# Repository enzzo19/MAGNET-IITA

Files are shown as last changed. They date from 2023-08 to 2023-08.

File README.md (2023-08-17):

# MAGNET-IITA SALTA 2023

Hola soy Enzo ! el Profe mentor del equipo IITA SALTA representando al [Instituto de Innovacion y Tecnologia Aplicada(IITA)](https://iita.com.ar/salta/) en la competencia [CANSAT](https://www.argentina.gob.ar/ciencia/sact/cansat-argentina) organizada por la el Ministerio de Ciencia, Tecnología e Innovación (MINCyT) y la Comisión Nacional de Actividades Espaciales [CONAE](https://www.argentina.gob.ar/ciencia/conae) en su edicion del año 2023, la idea de este repositorio es poder tener un lugar donde puedan encontrar el proceso y evolucion que fue siguiendo el equipo para cada una de las etapas de nuestra propuesta de CANSAT en su mision MAGNET-IITA.

## Etapas por describir

    * Presentacion / Mision Secundaria.
    * Diseño / Sistema de Descenso
    * Construccion
    * Estacion Terrestre
    * Pruebas

## Presentacion

El equipo IITA-Salta esta compuesto por los siguientes integrantes.

* **Gabriel Gutierrez**
* Rol en el equipo:
  * Encargado de Construccion
  * Encargado de Electronica

<p 
align="center">
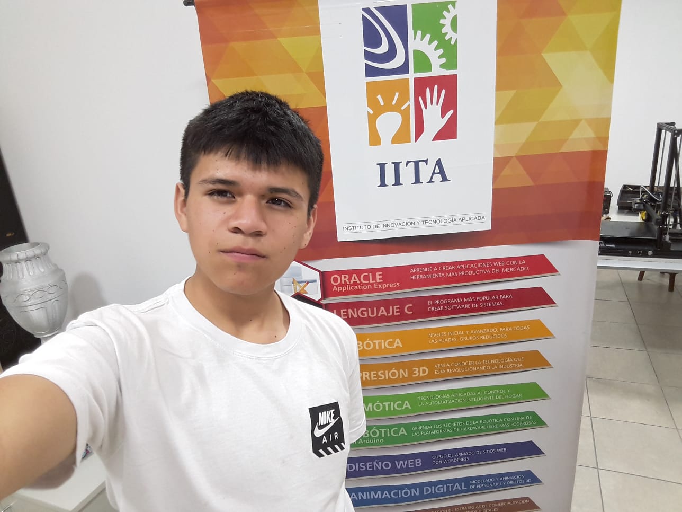
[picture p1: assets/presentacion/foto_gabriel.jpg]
Foto Gabriel

</p>

* **Morena Piren Castellanos**
* Rol en el equipo:
  * Encargado de Diseño 3D
  * Encargado de Sistema de Descenso
  * Ayudante de Construccion

<p 
align="center">
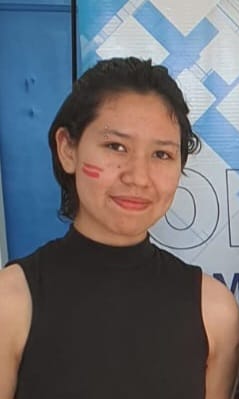
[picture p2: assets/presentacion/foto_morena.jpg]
Foto Morena

</p>

* **Daiana Andrea Saldria**
* Rol en el equipo:
  * Encargado de Estacion Terrestre
  * Encargada de Diseños p/ videos y Edicion
  * Ayudante de Construccion y Diseño

<p 
align="center">
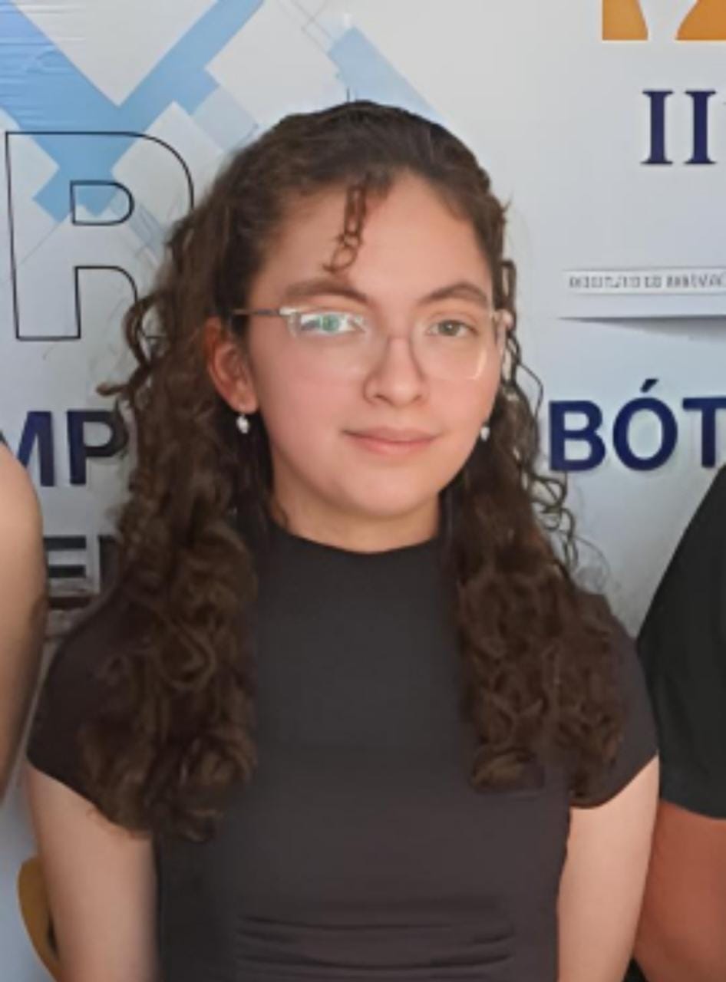
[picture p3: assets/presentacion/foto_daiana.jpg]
Foto Daiana

</p>

* **Iñaki Beccar Varela Goyechea**
* Rol en el equipo:
  * Encargado de Pruebas / Test
  * Ayudante en Construccion

<p 
align="center">
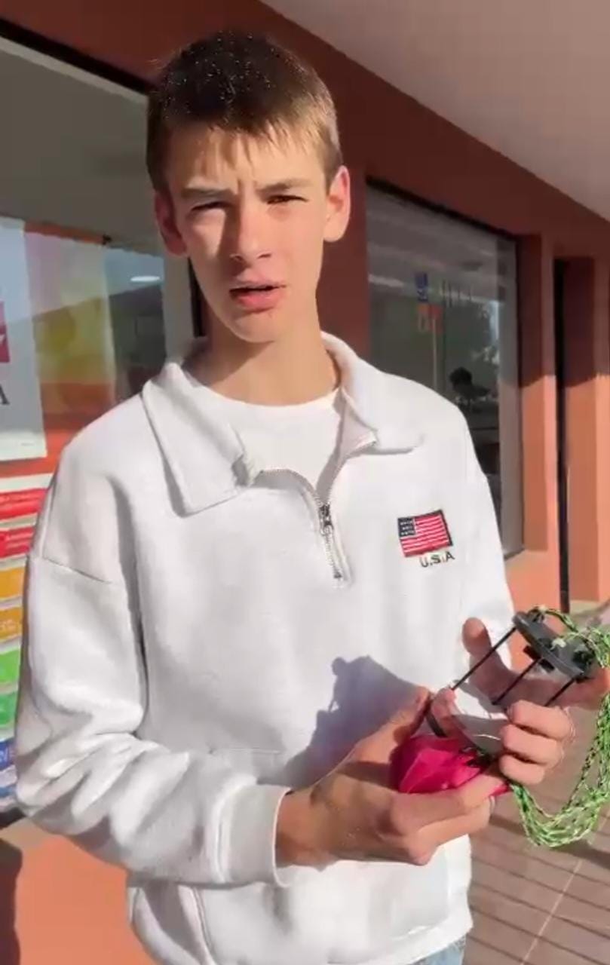
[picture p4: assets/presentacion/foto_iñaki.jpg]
Foto Iñaki

</p>

* **Esteban Yurkina**
* Rol en el equipo:
  * Mentor

<p 
align="center">
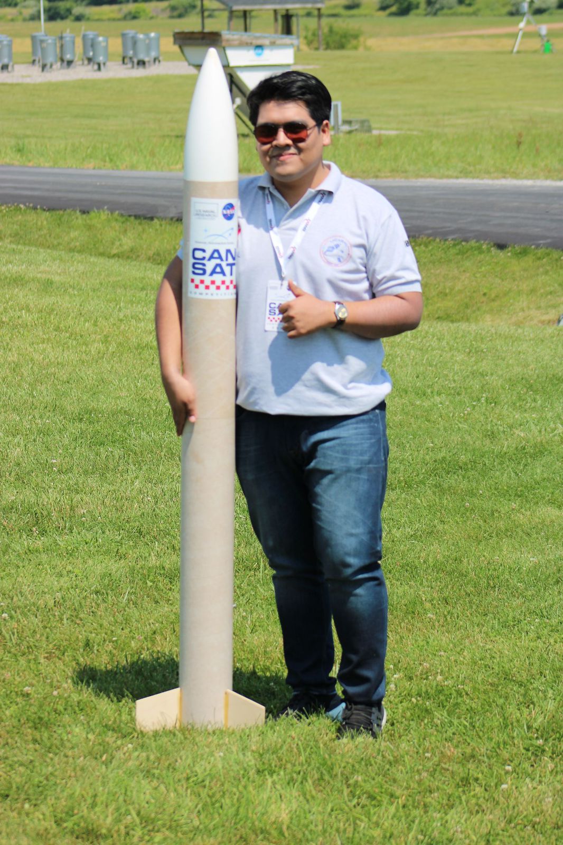
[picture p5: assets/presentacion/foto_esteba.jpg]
Foto Esteban

</p>

* Juarez Velazquez Enzo Jesus
* Rol en el equipo:
  * Profesor

<p 
align="center">
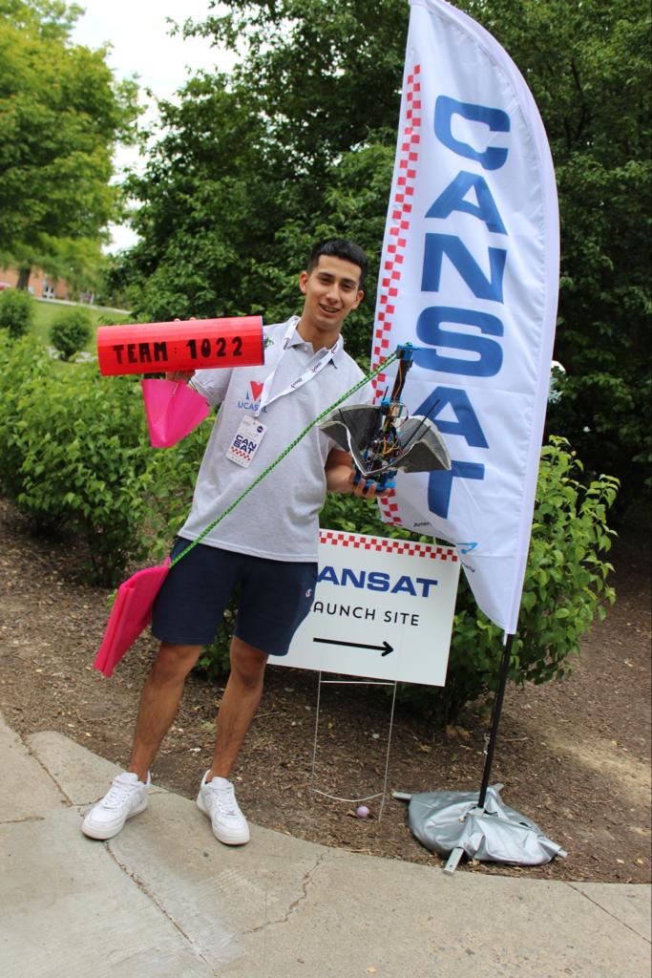
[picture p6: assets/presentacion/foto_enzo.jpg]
Foto Enzo

</p>

* Equipo Completo
<p 
align="center">
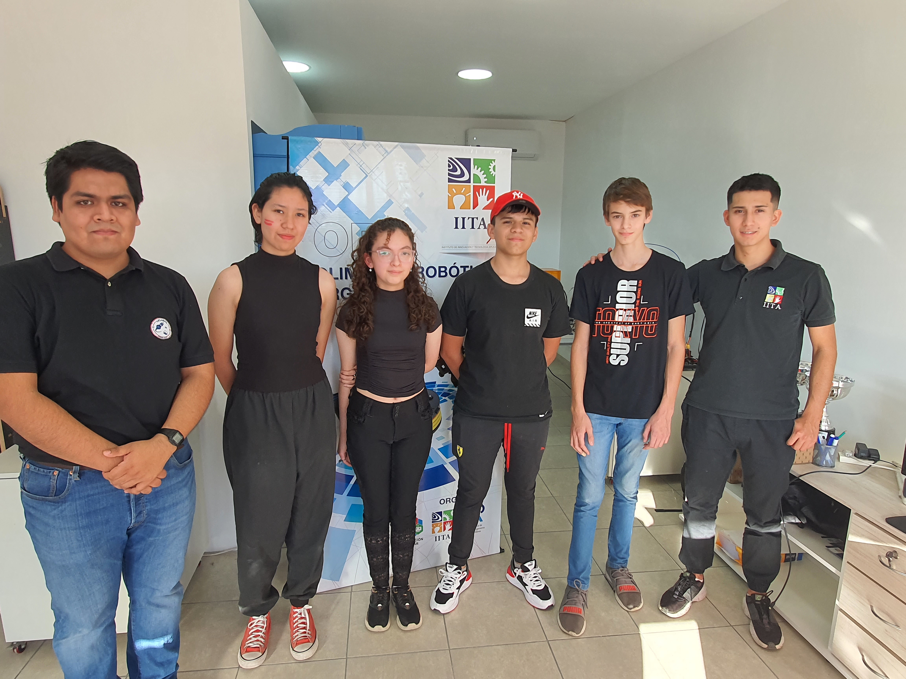
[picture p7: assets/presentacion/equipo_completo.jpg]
Foto Equipo

</p>

* Video de Presentacion [aqui](https://www.youtube.com/watch?v=Y_uPNAdjIT8)

## Nuestra Mision Secundaria:

Nuestro Cansat va a usarse para medir el campo magnético de la Tierra en diferentes altitudes y ubicaciones. Estos datos podrían usarse para estudiar el campo magnético de la Tierra y ayudar en una problemática ambiental de la región como la actividad sísmica y volcánica en nuestra provincia.

Esto es para nosotros una buena **MISIÓN** viéndolo como problemática ambiental, ya que Salta, es una región con una rica historia geológica y una importante actividad volcánica, por lo que estudiar las propiedades magnéticas del área podría ser un proyecto muy interesante y relevante.

Nuestro **ENFOQUE** será investigar el uso potencial de las mediciones de campos magnéticos para monitorear la actividad volcánica. Los cambios en el campo magnético pueden ser indicativos de actividad subterránea, por lo que desarrollar un sistema para medir y analizar datos de campo magnético en tiempo real podría ayudar a mejorar los sistemas de alerta sísmica temprana y monitoreo de volcanes.

## Diseño / Sistema de Descenso

## Encargada : Morena 

Para poder elegir el Diseño el equipo planeo en una reunion dibujando en una hoja, como deberia ser la forma del cilindro maximo que estaba permitido en la competencia, luego fueron agregando los componentes que necesitariamos para la mision primaria, sin conocer del todo aun las dimensiones reales de estos componentes, pero estimando y utilizando los datasheet e internet para poder hacer esas estimaciones lo mas realista posible, finalmente agregaron nuestro sensor a utilizar para la mision secundaria y tuvimos un primer boceto de como seria nuestro CANSAT.

<p 
align="center">
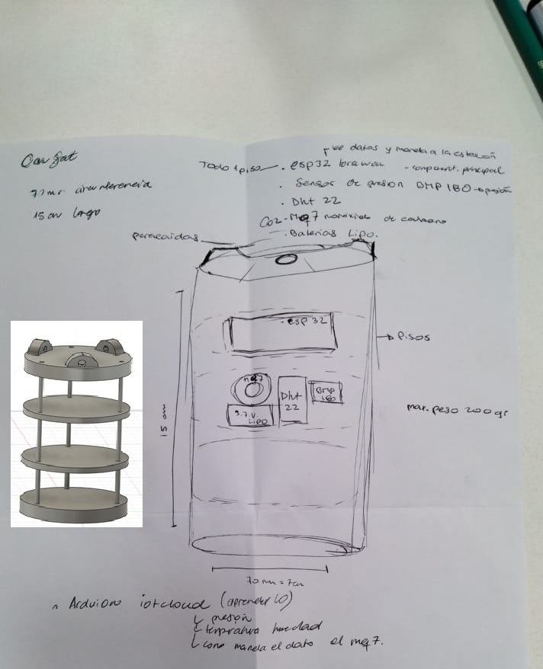
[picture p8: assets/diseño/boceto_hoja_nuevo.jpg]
Foto Boceto

</p>

En esta etapa fue crucial la [capacitacion Virtuales de la CONAE](https://www.youtube.com/watch?v=Zfl7T_GsNHY&list=PLGYpcbdUKl0F0Re8deZHd4bWShjPOa0xN&pp=iAQB) que tomamos para poder definir algunas cuestiones importantes de nuestra primera aproximacion en la cual los chicos con cada topico diferente que veian en las clases, decidian agregar, sacar o modificar alguna parte de nuestro DISEÑO por recomendacion de los expertos.

### Piezas 3D

Para poder realizar piezas personalizadas, decidimos utilizar tecnologia de Impresion3D ya que Morena hace poco habia podido comprar una y queria aprovechar para aprender a diseñar sus propias piezas, tambien por que en el Instituto contamos con una gran variedad de impresoras 3D y nos seria facil poder tener piezas para probar.

Asi fue como decidieron que las piezas a diseñar iban a ser:

* La Base
* El Tope
* Las piezas de anclaje del sistema de descenso
* Las Varillas de Separacion de Niveles

Estas piezas fueron teniendo una serie de modificaciones hasta llegar a la version Final de cada una ya que con cada prueba Morena fue adquiriendo experiencia sobre la forma que debia tener para que sean utiles.

La version Final de cada pieza la pueden encontrar en esta [carpeta](https://github.com/enzzo19/MAGNET-IITA/tree/main/Piezas%203D).

### Evolucion del Diseño

#### Paracaidas

El Paracaidas tiene las dimensiones de **25cm** de diametro con un **orificio de derrame** o **orificio de ventilacion** y Daiana se encargo de hacer los calculos para poder conseguir o diseñar el correcto.

<p 
align="center">
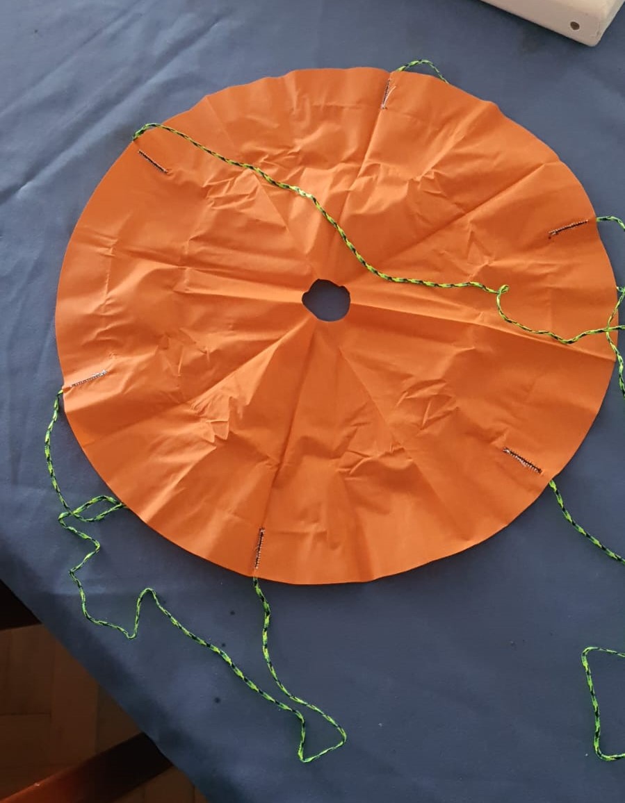
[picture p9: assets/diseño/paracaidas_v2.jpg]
Foto Evolucion Diseño

</p>

#### Pieza Tope del Cansat
Como vieron en el boceto la primera idea de los chicos fue agarrar el paracaidas de un solo lugar en el centro y tirarlo como si fueran los **Soldaditos de Juguete**
<p 
align="center">
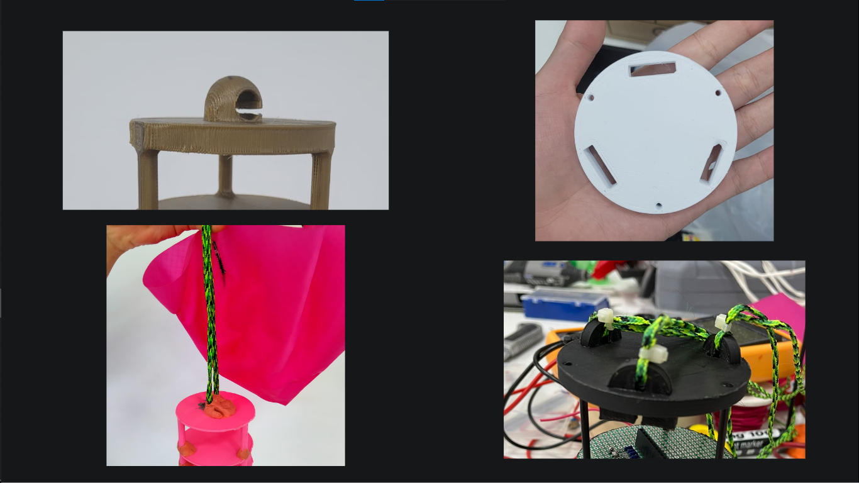
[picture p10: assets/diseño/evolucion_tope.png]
Foto Evolucion Diseño

</p>

Esto no resulto del todo bien y decidieron cambiarlo por un sistema donde tiene 3 puntos de agarre y cada cordon esta separado lo que ayudo a que el paracaidas se despliegue de la forma correcta y no se enredaran los cordones, esta misma pieza tiene el proposito de soportar las varillas de fibra de Carbono de la Estructura.

#### Piezas de Agarre del Cordon de los Paracaidas

Con las piezas que sujetan los cordones del paracaidas tuvieron que rediseñarla ya que a las primeras debian hacerle un corte con el minitorno para poder encajar los cordones y eso suponia un punto debil en los agarres, y asi quedo como se aprecia en la imagen a la derecha con un orificio en la parte baja para pasar el cordon y solo poner la pieza haciendo click sobre el tope.

<p 
align="center">
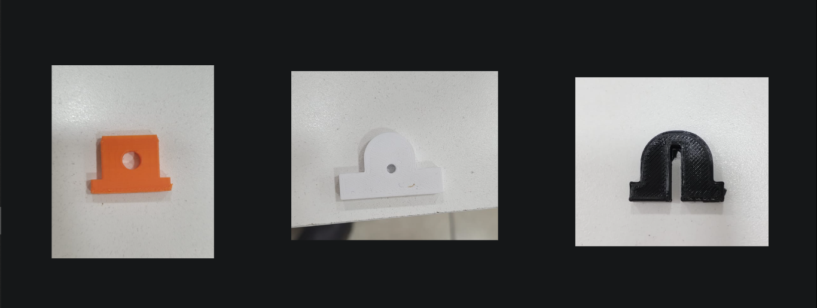
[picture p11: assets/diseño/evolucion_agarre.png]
Foto Evolucion Diseño

</p>

#### Varillas de Separacion de Niveles
Esta pieza no la tenian prevista en el diseño hasta realizaron las pruebas de Vibracion mas adelante explico por que decidieron ponerle eso al modelo Final !!

<p 
align="center">
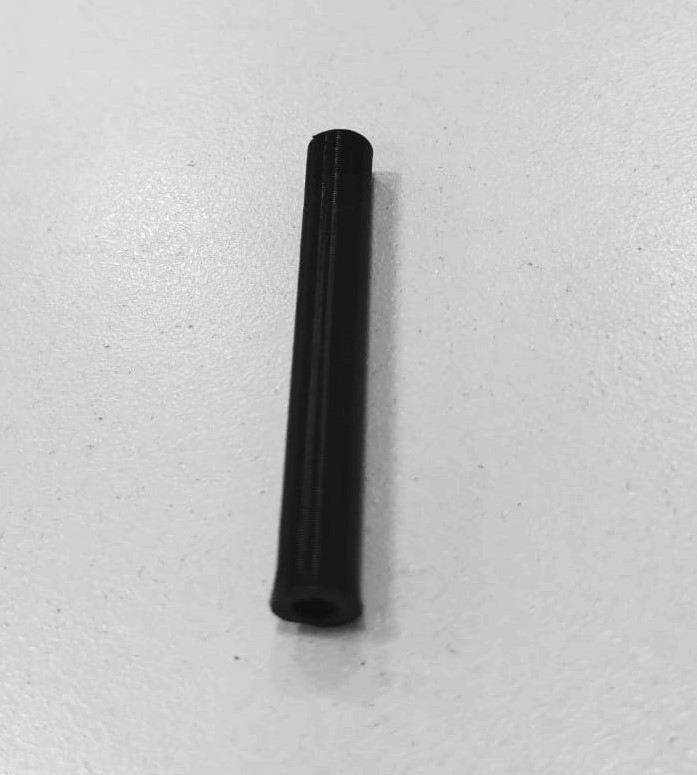
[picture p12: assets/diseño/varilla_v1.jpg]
Foto Evolucion Diseño

</p>

## Construccion
## Encargado: Gabriel

### Lista de Materiales:

* 1 - Heltec ESP32 Lora V2
  <p 
  align="center">
  Foto Evolucion Diseño
  </p>
* 1 - Sensor BMP180
  <p 
  align="center">
  Foto Evolucion Diseño
  </p>
* 1 - SensorDHT22
  <p 
  align="center">
  Foto Evolucion Diseño
  </p>
* 1 - Sensor MPU9250
  <p 
  align="center">
  Foto Evolucion Diseño
  </p>
  
* 2 - Placas perforadas 10x10cm
  <p 
  align="center">
  Foto Evolucion Diseño
  </p>
* 3 - Varilla de Fibra de Carbono de 3mm de diametro y 12 cm de largo
  <p 
  align="center">
  Foto Evolucion Diseño
  </p>
* 1 - Regulador de Tension 7805
  <p 
  align="center">
  Foto Evolucion Diseño
  </p>

* 1 - Switch ON/OFF
  <p 
  align="center">
  Foto Evolucion Diseño
  </p>

### Diagrama Electrico
Para realizar el Diagrama electrico usaron EasyEDA en esta parte es donde mas ayuda necesitaron, la idea fue que Gabriel con la ayuda de Iñaki vallan construyendo los circuitos en Protoboard, probando primero el funcionamiento de los sensores de forma Individual y luego ir acoplando todo en un solo firmware para el CANSAT
<p 
align="center">
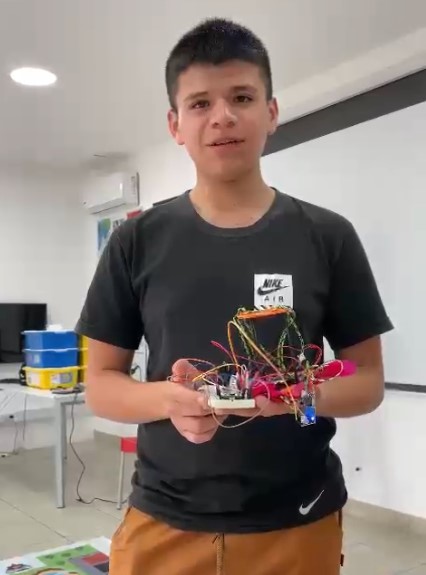
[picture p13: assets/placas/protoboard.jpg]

</p>
Una vez estaban seguros de que los circuitos electronicos funcionaban en la Protoboard y el CANSAT cumplia con la Transmision de datos tanto para la mision Primaria como la Secundaria empezaron a hacer los circuito Electricos.
<p 
align="center">
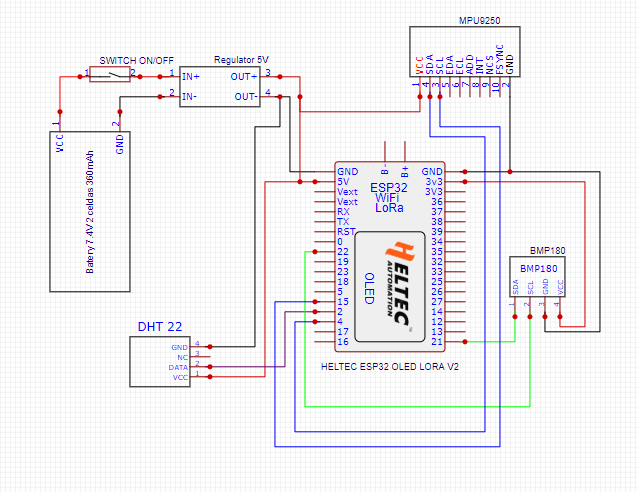
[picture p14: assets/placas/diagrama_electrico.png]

</p>

Los profes los ayudamos con el diseño de Placas en PCB personalizadas, que mandamos a pedir, que era por ahi lo que pensabamos que se iba a complicar mas, pero lo terminaron haciendo ellos sin problemas ya que entendieron como posicionar los componentes y rutear todo, asi que solo nos quedo la tarea de corroborar que su diseño no hacia un cortocircuito.

### PCB Personalizados

* Base con agujeros
<p 
align="center">
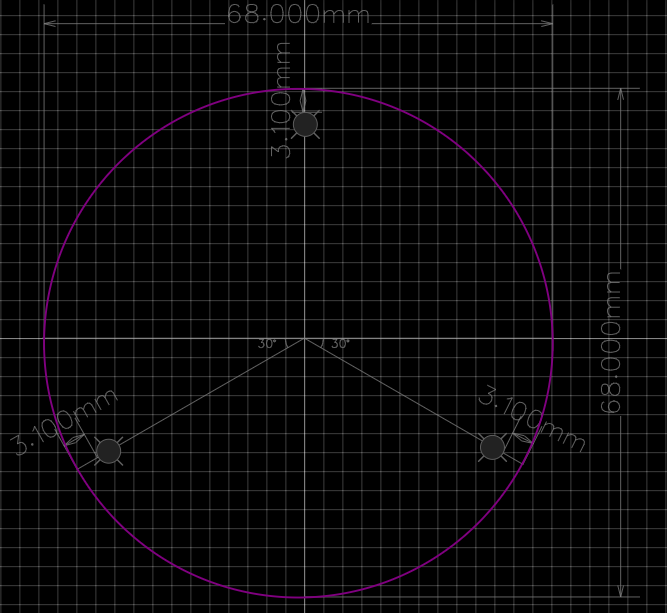
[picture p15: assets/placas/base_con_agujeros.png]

</p>

* Piso 1 Componentes
<p 
align="center">
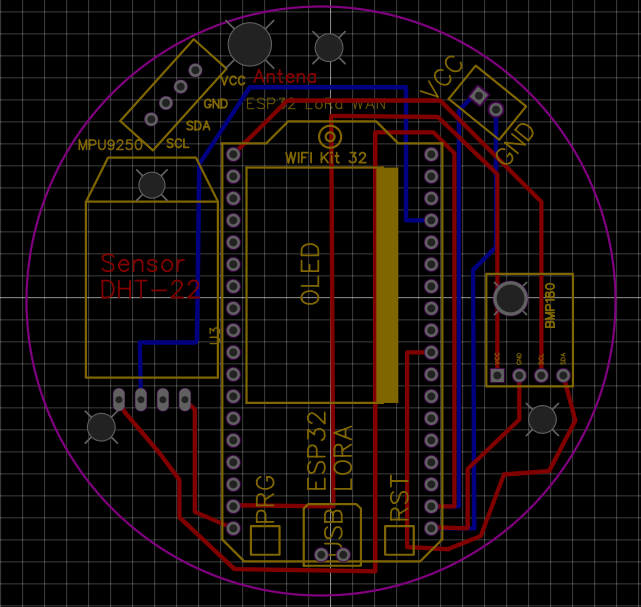
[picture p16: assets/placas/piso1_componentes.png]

</p>

* Piso 2 Mision Secundaria
<p 
align="center">
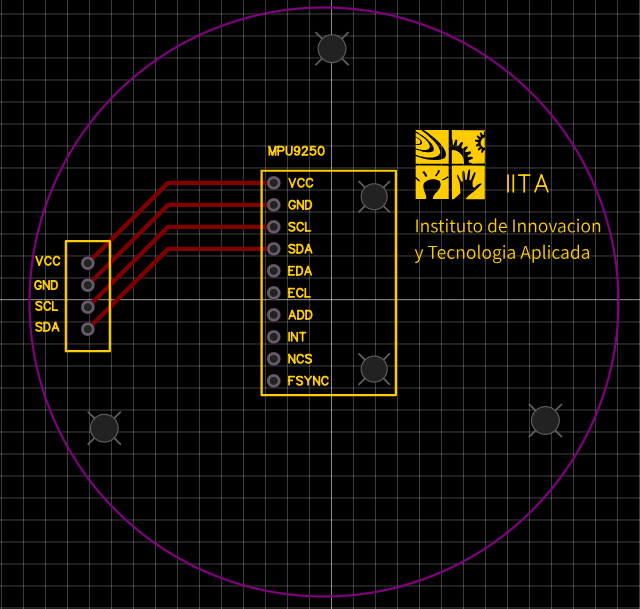
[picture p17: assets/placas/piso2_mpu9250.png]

</p>

## Construccion del CANSAT
Esperando que lleguen las placas pasaba el tiempo y la presentacion se nos venia encima, por lo que decidimos no confiarnos por que sino nos quedariamos sin poder terminar ni probar el CANSAT y decidimos realizar a mano en placas experimentales perforadas, todo el diseño de los circuitos electronicos para nuestro CANSAT, esto fue un gran trabajo por parte de Gabriel que tiene muy buenas habilidades para soldar, y con las herramientas manuales, nos conto que es debido a que ayuda a su papa en un taller de AudioCAR y Electronica.

<p 
align="center">
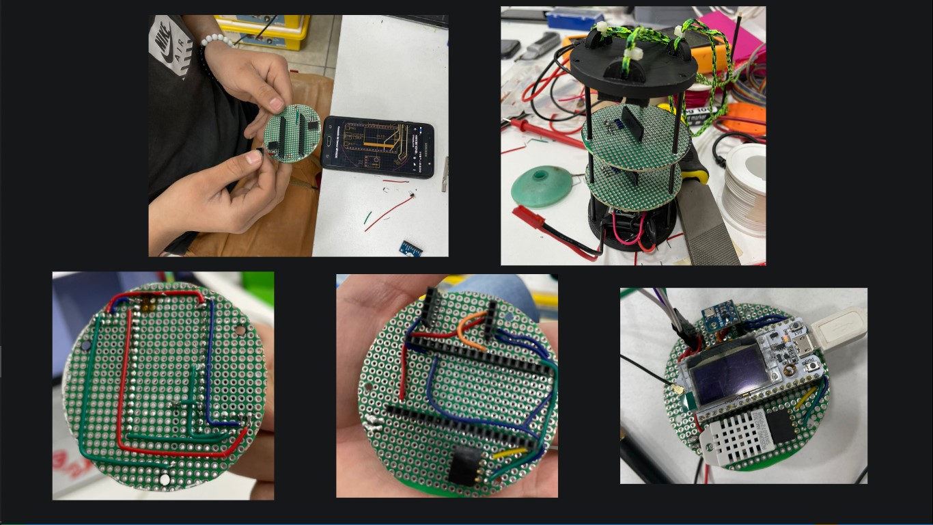
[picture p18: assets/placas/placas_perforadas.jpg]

</p>

## CANSAT TERMINADO

Despues de Terminar solo quedaban ponerle los cables que unian los pisos del CANSAT y estaba listo para poder comenzar a realizar las Pruebas de Funcionamiento.

<p 
align="center">
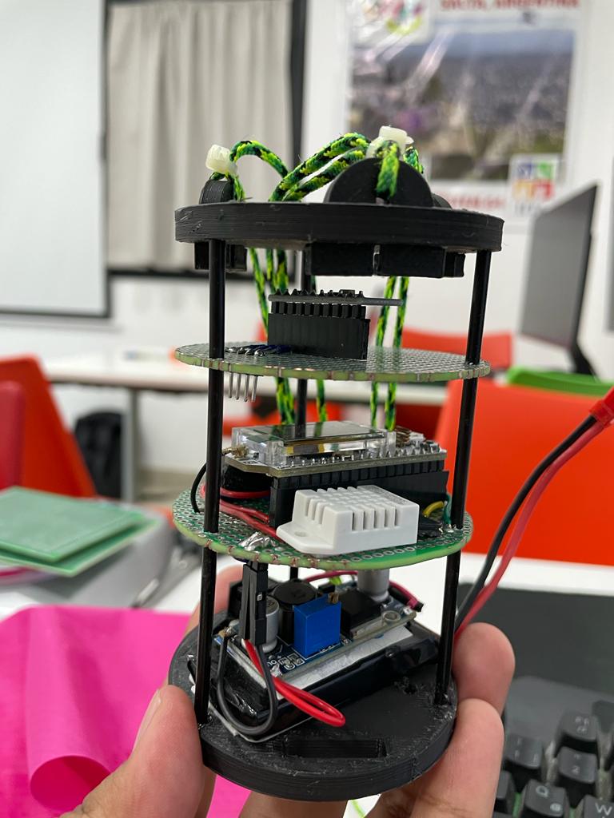
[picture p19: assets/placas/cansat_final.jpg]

</p>

## Estacion Terrestre

## Encargada: Daiana

Para poder programar la estacion terrestre como el firmware del Modulo que seria receptor de los datos Daiana tuvo que aprender a programar en Arduino ya que cuando comenzo contaba con mas habilidades en Python y para poder mejorar y facilitar la experiencia los profes le recomendamos utilizar [Arduino Iot Cloud](https://cloud.arduino.cc/) ya que nos ofrecia la ventaja de que con una especie de Drag and Drop tener una estacion Terrestre Visualizando los datos y algunas graficas en Tiempo Real por lo que solucionaba la parte Grafica, y si costaba un poco aprender a usarlo pero merecia la pena.

* Version Web

Visualizando en Tiempo Real los Datos
<p 
align="center">
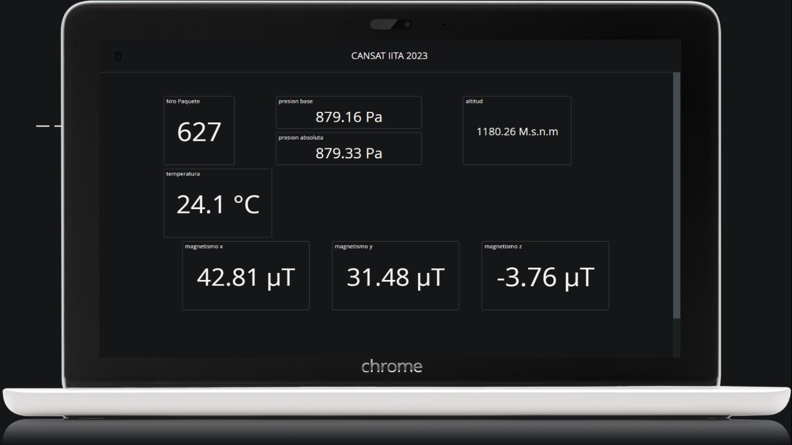
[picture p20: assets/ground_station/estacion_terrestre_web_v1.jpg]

</p>

Visualizando Grafica en Tiempo Real los Datos
<p 
align="center">
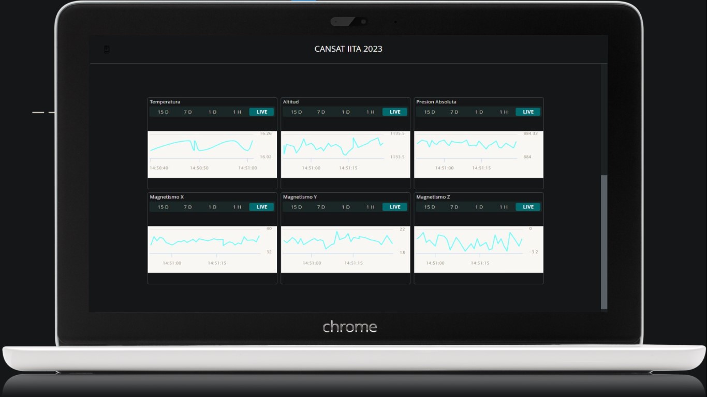
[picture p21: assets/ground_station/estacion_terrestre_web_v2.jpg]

</p>

## Version Movil
<p 
align="center">
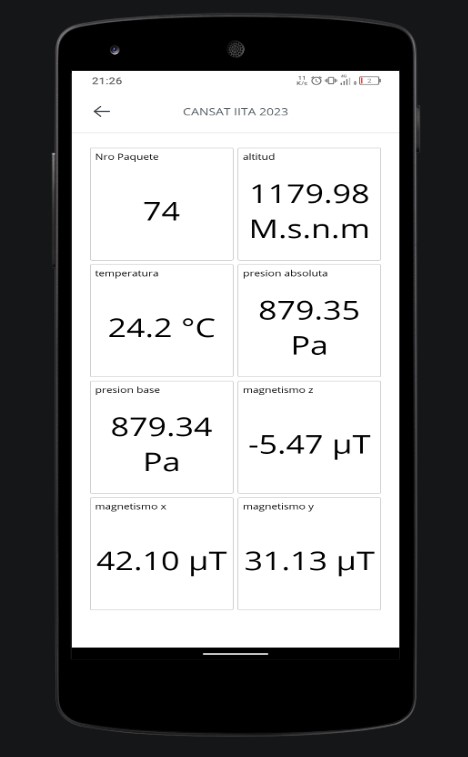
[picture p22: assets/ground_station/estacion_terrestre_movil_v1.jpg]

</p>

Cuando teniamos funcionando la Estacion Terrestre con Arduino IoT Cloud preguntamos en el foro si era posible tener Wi-Fi en el lugar de lanzamiento o Red de Datos Moviles y nos dijeron que no nos lo aseguraban por lo que es un lugar alejado, esto ya que lo que estabamos usando utilizaba internet para mandar los datos desde nuestro Modulo receptor hacia Arduino IoT Cloud, por recomendacion, decidimos que Daiana haga una estacion Terrestre en Python que lea los datos del puerto Serial, se los pueda visualizar y los guarde en archivos, con esto Dai pudo aprovechar para profundizar un poco mas su conocimiento en Python pero era una tarea contrarreloj para poder tenerlo funcionando.

### Version Escritorio

<p 
align="center">
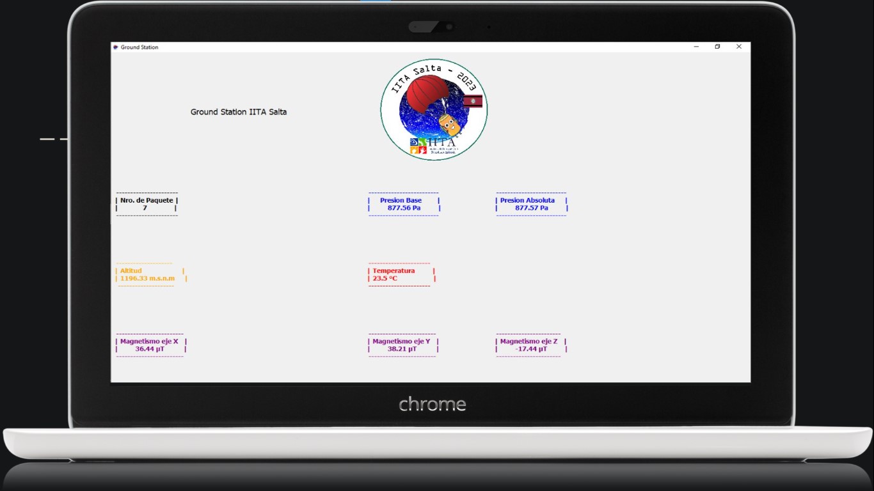
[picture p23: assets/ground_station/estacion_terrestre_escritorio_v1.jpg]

</p>

Los archivos que guarda son un archivo descriptivo y uno para analizarlo, pero aun no pudimos llegar a tener datos para analiar por lo que vamos a contar en los Test.

<p 
align="center">
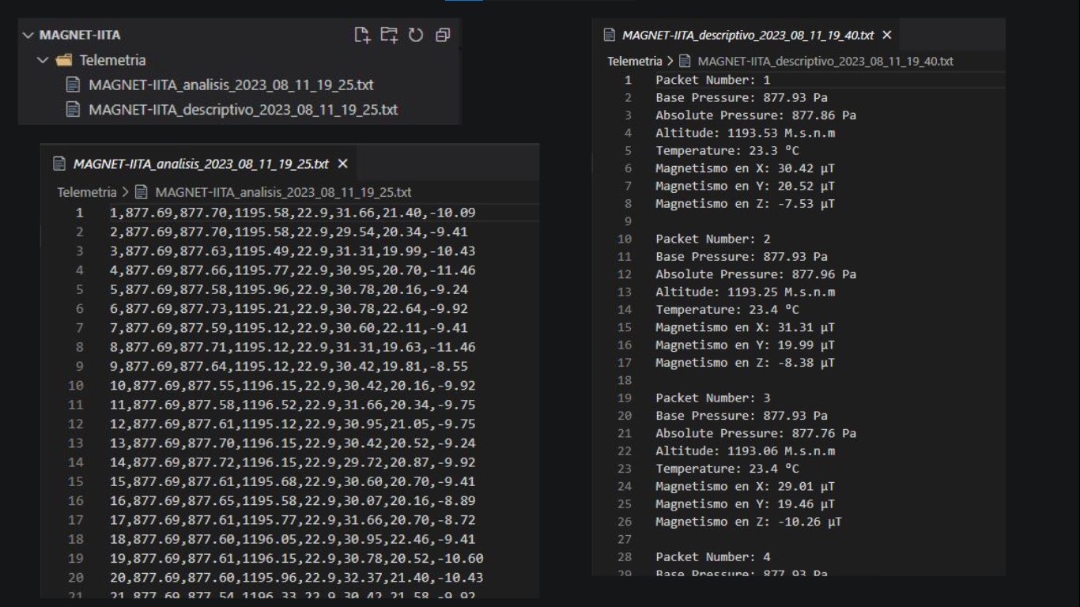
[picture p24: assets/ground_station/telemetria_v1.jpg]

</p>

## Pruebas / Test de Funcionamiento

## Encargado: Iñaki

## Prueba de Temperatura

Elementos utilizados:

* Taper Termico de Tergopor
* Pistola de Calor

Procedimiento:

1. Encender la estacion Terrestre y el CANSAT y registrar la temperatura antes de la prueba.
2. Colocar el CANSAT dentro del recipiento Termico y sellarlo.
3. Encender la Pistola de Calor y colocarla e el orificio del recipiente Termico.
4. Esperar 2 minutos y verificar si se visualiza el incremento de Temperatura.
5. Quitar la Pistola de calor.
6. Esperar 2 Minutos y visualizar si la Temperatura se vuelve a estabilizar a como estaba entes de la prueba.

<p 
align="center">
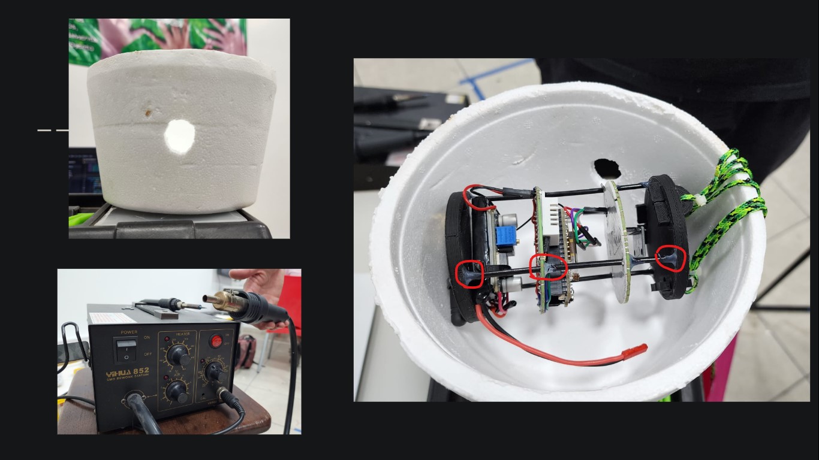
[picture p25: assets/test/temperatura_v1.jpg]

</p>

[Link de Video de Prueba de Temperatura](https://youtu.be/VTKC8T8OjOQ)

Conclusion:

Pudimos corroborar el correcto funcionamiento de nuestro Sensor de Temperatura, y que la estacion Terrestre visualiza los datos de la prueba, sin embargo tambien nos sirviopara darnos cuenta que el pegamento que estabamos utilizando (POXIPOL) no era el mejor para este tipo de uso asi que decidimos cambiarlo por la Gotita.

## Prueba de Presion / Vacio

Elementos utilizados:

* Globo
* Botella cortada a la Mitad
* Cinta Multiuso de Alta Resistencia
* Aspiradora de Mano

Procedimiento:

1. Encender la estacion Terrestre y el CANSAT y registrar la presion Absoluta antes de la prueba.
2. Colocar el CANSAT dentro del recipiento de vacio y sellarlo.
3. Encender la Aspiradora de mano.
4. Esperar 2 minutos y verificar si se visualiza la disminucion de Presion.
5. Apagar la Aspiradora de mano.
6. Esperar 2 Minutos y visualizar si la Presion Absoluta se vuelve a estabilizar a como estaba entes de la prueba.

<p 
align="center">
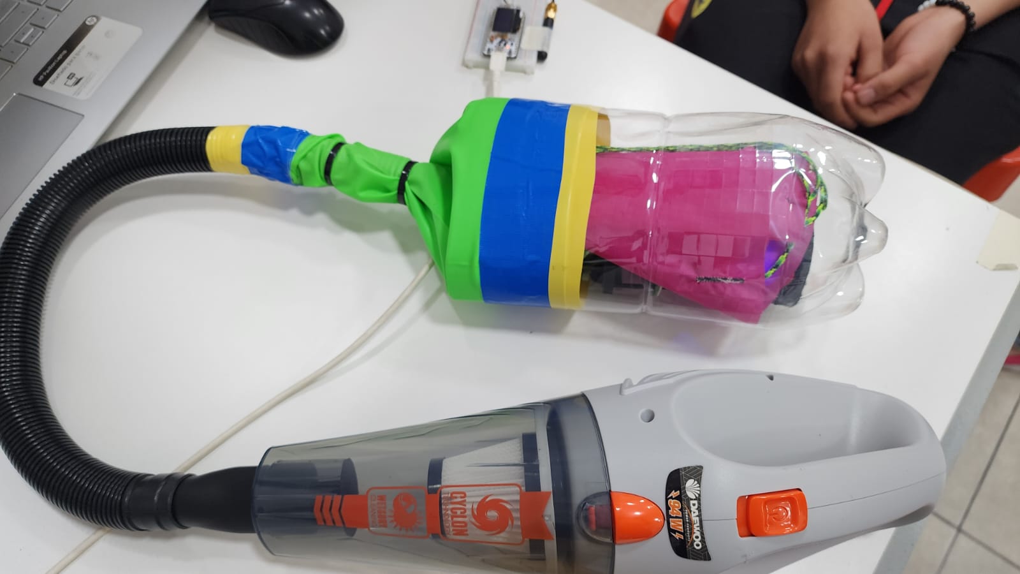
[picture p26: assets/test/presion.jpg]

</p>

Conclusion:

Pudimos corroborar el correcto funcionamiento de nuestro Sensor de Presion, y que la estacion Terrestre visualiza los datos de la prueba, sin embargo hubera estado mejorpoder hacer la prueba con una olla a presion o con una Aspiradora Industrial, y necesitabamos sellar bien el recipiente contenedor.

# Prueba de Vibracion

Elementos Utilizados:

* Lijadora Electrica
* Precintos
  
Procedimiento:

1. Encender la estacion Terrestre y el CANSAT y registrar el enviado de los datos de Telemetria antes de la prueba.
2. Fijar el CANSAT a la Lijadora con los precintos.
3. Encender la Lijadora.
4. Esperar 2 minutos.
5. Apagar la Lijadora.
6. Esperar 2 Minutos y visualizar el estado de funcionamiento del CANSAT y la integridad de sus partes.

<p 
align="center">
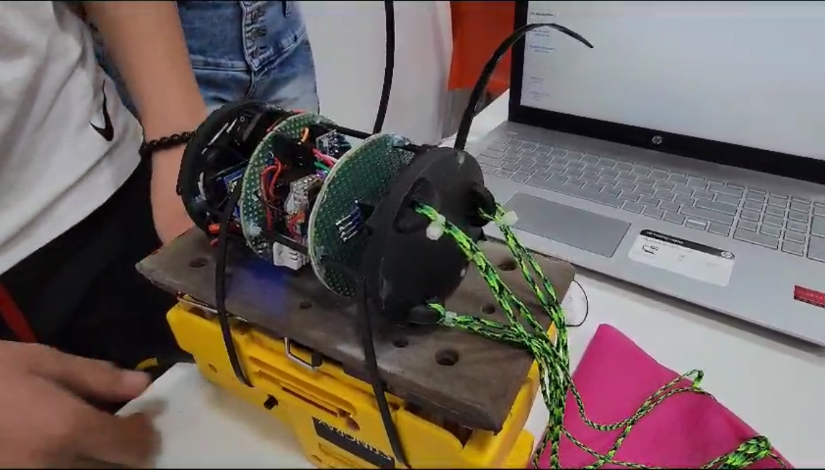
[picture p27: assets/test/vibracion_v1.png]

</p>

[Video de Prueba de Vibracion](https://youtu.be/Py2hboB3tCM)

Conclusion:

Pudimos corroborar el correcto funcionamiento de nuestro CANSAT sin embargo la Vibracion de la Maquina hizo que los placas perforadas empiecen a deslizarse por las varillas de Fibra de Carbono, por lo que Morena tuvo que diseñar las Varillitas Separadoras que mostramos al principio para pode darle una mayor estabilidad, tambien aseguramos las conexiones de los pines con silicona para asegurarlas y la bateria y la antena con un precinto y cinta doble-fax, esta prueba aunque parecia menor resulto ser la que nos demando que aseguremos la Estructura de nuestro CANSAT.

## Prueba de Caida

Elementos Utilizados:

* Un pedazo de hilo o cuerda de entre 60cm y 80cm
* Una base firme con una altura de aprox 2m
  
Procedimiento:

1. Encender la estacion Terrestre y el CANSAT y registrar el enviado de los datos de Telemetria antes de la prueba.
2. Fijar el CANSAT desde la mitad de los cordones del paracaidas a un extremo de la cuerda.
3. Fijar el otro extremo de la cuerda a la base firme desde donde se o va alanzar.
4. Soltar la cuerda.
5. Visualizar el estado de funcionamiento del CANSAT y la integridad de sus partes.

<p 
align="center">
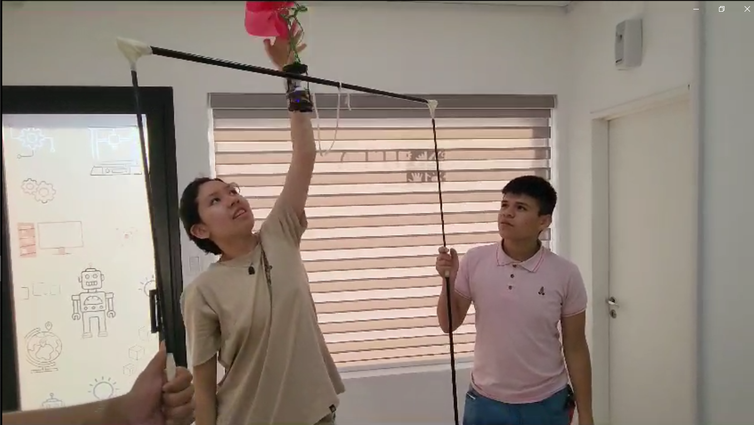
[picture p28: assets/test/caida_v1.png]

</p>

[Video de Prueba de Caida](https://youtu.be/lD-E8avi6yo)

Conclusion:

Pudimos corroborar el correcto funcionamiento de nuestro CANSAT aguanto la prueba de Caida y todas las partes siguieron en una sola pieza mientras continuaba transmitiendo los datos a la estacion terrestre.

## Prueba de Peso:

Elementos Utilizados:

* Balanza
  
Procedimiento:

1. Encender la Balanza y esperar a que marque 0Kg.
2. Colocar cada parte del CANSAT por encima de la Balanza.
3. Registrar la medicion.

<p 
align="center">
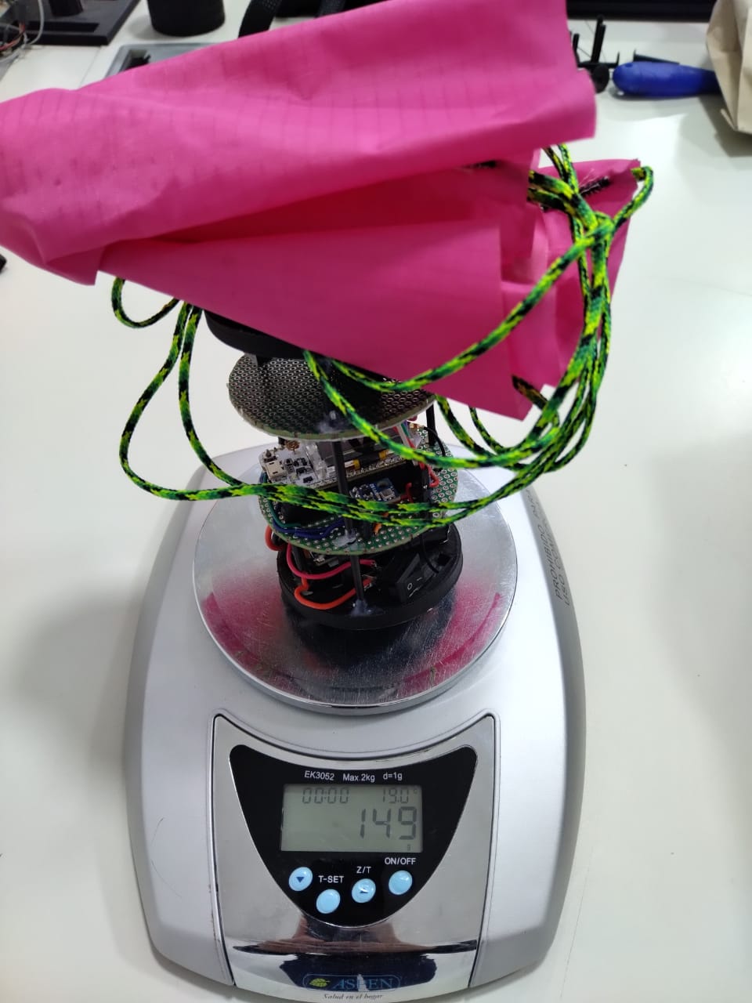
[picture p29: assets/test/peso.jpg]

</p>

Conclusion:

Pudimos corroborar que nuestro CANSAT con todos los componentes que utiliza se encunetra dentro de los margenes de la competencia.

## Prueba de Vuelo / Lanzamiento

Para poder corroborar el funcionamiento realizando una prueba lo mas Real posible, decidimos utilizar un Dron de gran porte capaz de llevar pesos livianos y que contara con un Tren de Aterrizaje desplegable, para eso nos dirigimos hacia la [CADAER club de amigos del Aeromodelismo](https://goo.gl/maps/sKJwR8qwuQN4Q6Yu9) este es un campo donde realizan pruebas de lanzamientos, pilotan aviones a escala de modelismo, donde estamos muy agradeidos por el buen trato que nos brindaron ya que aparte de realizar nuestra prueba tambien pudimos aprender sobre el Hobby del Aeromodelismo.

Elementos Utilizados:

* Dron
*  Precintos
*  Tubos de PVC de distinto diametro.
  
Procedimiento:

1. Utilizando el Tren Retractil del Dron armamos un mecanismo que al elevarse cuando el piloto levante las patitas de aterrizaje, nuestro CANSAT que va enganchado pueda caer.

<p 
align="center">
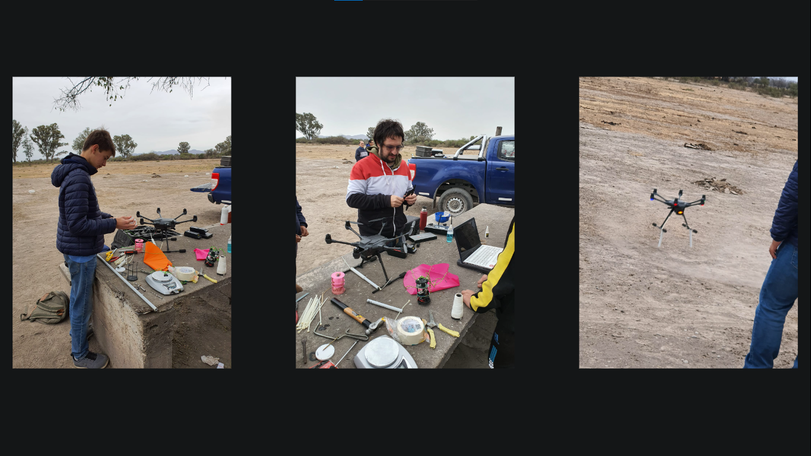
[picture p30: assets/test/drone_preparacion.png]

</p>

2. Encender la estacion Terrestre, asegurar el CANSAT al Mecanismo y registrar el enviado de los datos de Telemetria antes de la prueba.

<p 
align="center">
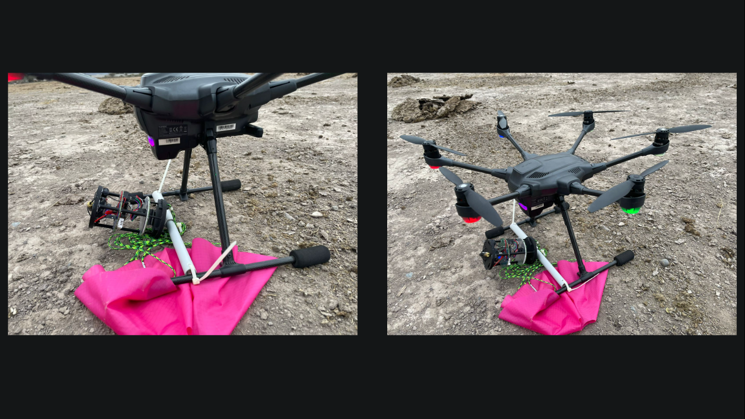
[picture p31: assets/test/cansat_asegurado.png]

</p>

3. Elevar el Dron junto con el CANSAT y registrar la medida de Altitud en la estacion Terrestre.

<p 
align="center">
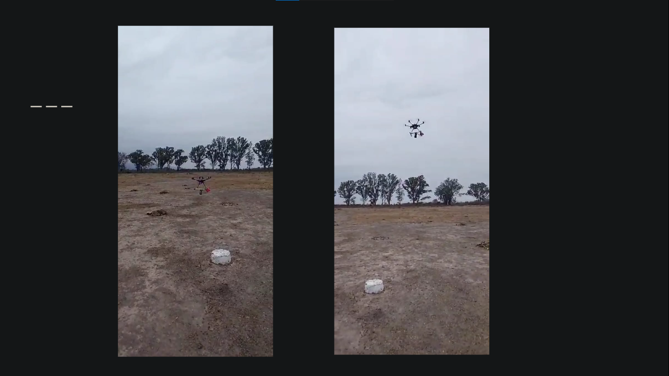
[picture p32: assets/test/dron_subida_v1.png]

</p>

4. Soltar el CANSAT a una altura entre 100m y 200m para poder corroborar el funcionamiento del sistema de Descenso y que continua enviando datos a la estacion terrestre.

Conclusion:

Mientras haciamos las pruebas el Piloto del Dron perdio el Control desde el mando, y nuestro CANSAT como su DRON cayeron desde aproximadamente 60m ya que no habia llegado a desplegar las patitas retractiles por lo que se vinieron en picada juntos y el CANSAT sufrio algunos daños.

<p 
align="center">
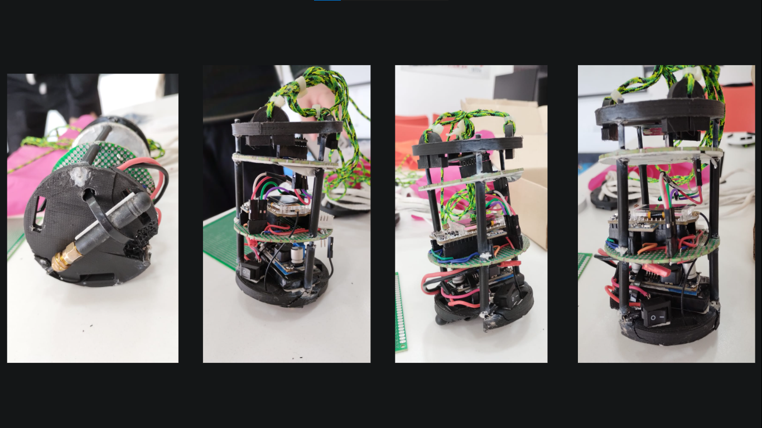
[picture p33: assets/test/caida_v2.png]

</p>

[Prueba de Vuelo con Dron](https://youtu.be/d7HWgFIUXFQ)

[Fail de la Prueba de Vuelo con Dron](https://www.youtube.com/shorts/WMEe1llR1y4)

Pero aunque parece algo malo estas pruebas nos sirvieron para darnos cuenta y aprender de lo siguiente:

* Realizar los Test previos al Drone fue muy bueno ya que ahi fue que aseguramos la estructura, y eso hizo que el CANSAT sufra daños menores.

* Nuestra Estacion Terrestre continua recibiendo datos desde la altura tanto la version web como movil  de escritorio

* Cuando conectamos la Electronica vimos que el regulador que estabamos usando era demasiado fragil, ya que se le desoldaron los capacitores y esto hizo que se pierda la energia, por lo que decidimos cambiarlo por un regulador de Tension 7805.

* Teniamos ya sensores y piezas de repuestos, por lo que reconstruir el CANSAT nos llevo muy poco tiempo y ya contamos con uno totalmente funcional, aparte esperamos tener uno mas completo como repuesto.

## CONCLUSION

Estamos muy agradecidos por permitirnos participar en la competencia y por todo el aprendizaje y experiencia que nos brindaron desde el comienzo, por el feedback enviado tanto desde la plataforma para poder solucionar nuestros inconvenientes como el de Florencia Moya nuestra tutora que estuvo pendiente de nuestros avances a lo largo de la competencia, esperamos poder reunirnos con ustedes y realizar una prueba de lanzamiento real y asi crear un espacio mas en este repositorio y seguir sumando experiencias llenas de aprendizaje.

**El cohete ruge, la emoción se eleva, y el viaje espacial se convierte en realidad.**

<p 
align="center">
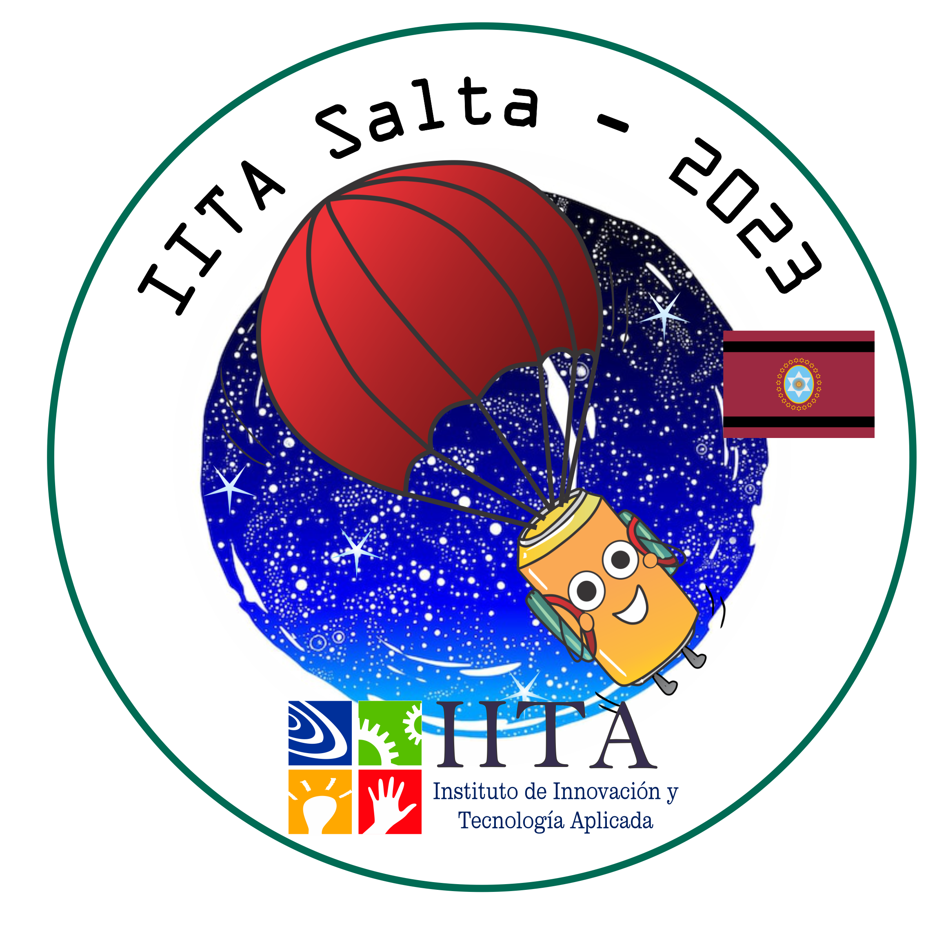
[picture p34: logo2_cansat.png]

</p>

Equipo: IITA-SALTA (18864681).

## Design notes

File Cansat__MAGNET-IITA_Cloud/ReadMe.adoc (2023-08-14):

:Author: enzzo19
:Email:
:Date: 06/08/2023
:Revision: version#
:License: Public Domain

= Project: {Project}

Describe your project

== Step 1: Installation
Please describe the steps to install this project.

For example:

1. Open this file
2. Edit as you like
3. Release to the World!

== Step 2: Assemble the circuit

Assemble the circuit following the diagram layout.png attached to the sketch

== Step 3: Load the code

Upload the code contained in this sketch on to your board

=== Folder structure

....
 sketch123                => Arduino sketch folder
  ├── sketch123.ino       => main Arduino file
  ├── schematics.png      => (optional) an image of the required schematics
  ├── layout.png          => (optional) an image of the layout
  └── ReadMe.adoc         => this file
....

=== License
This project is released under a {License} License.

=== Contributing
To contribute to this project please contact: 

=== BOM
Add the bill of the materials you need for this project.

|===
| ID | Part name      | Part number | Quantity
| R1 | 10k Resistor   | 1234-abcd   | 10       
| L1 | Red LED        | 2345-asdf   | 5        
| A1 | Arduino Zero   | ABX00066    | 1        
|===

=== Help
This document is written in the _AsciiDoc_ format, a markup language to describe documents. 
If you need help you can search the http://www.methods.co.nz/asciidoc[AsciiDoc homepage]
or consult the http://powerman.name/doc/asciidoc[AsciiDoc cheatsheet]

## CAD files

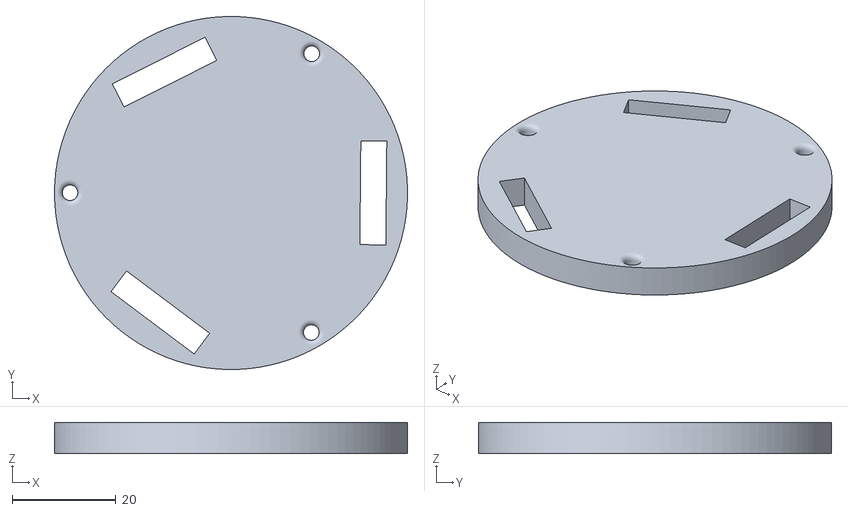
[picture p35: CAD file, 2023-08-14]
Piezas 3D/BASE.stl
68.0 x 68.0 x 6.00

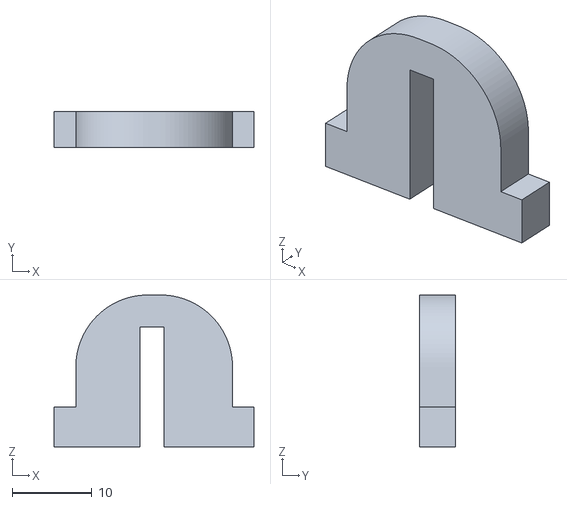
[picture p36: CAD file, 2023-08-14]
Piezas 3D/PIEZA v1.stl
25.0 x 4.50 x 19.0

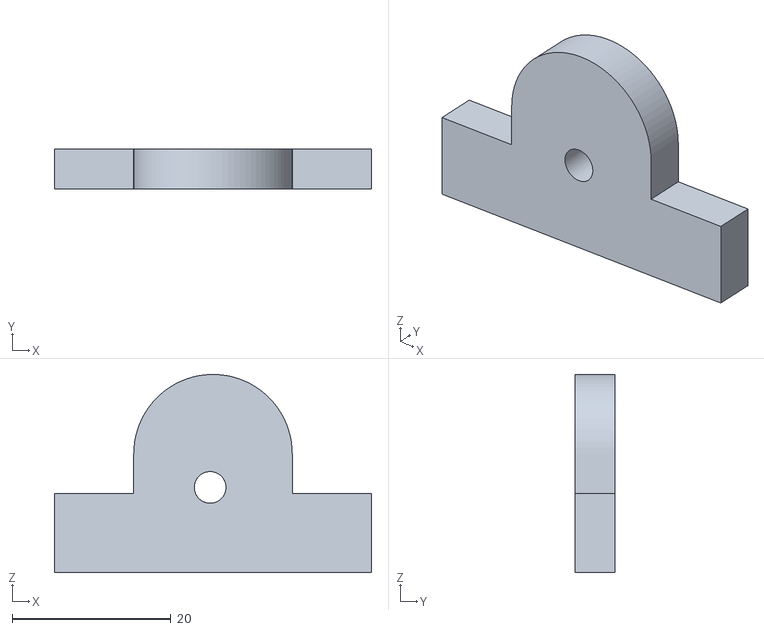
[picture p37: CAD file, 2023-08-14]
Piezas 3D/Sin título v1.stl
40.0 x 5.00 x 25.0

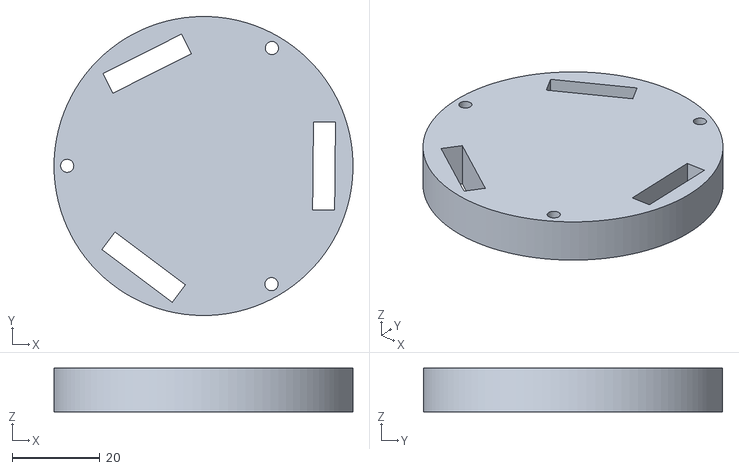
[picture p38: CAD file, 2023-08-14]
Piezas 3D/bbbbbbbbbbbase.stl
68.0 x 68.0 x 10.0

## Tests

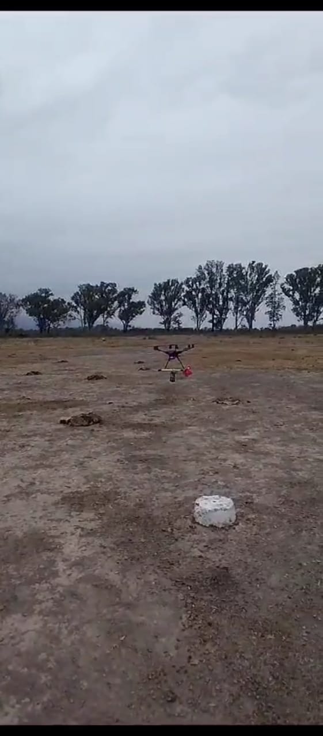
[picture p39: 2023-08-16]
assets/test/dron_subida2.jpg

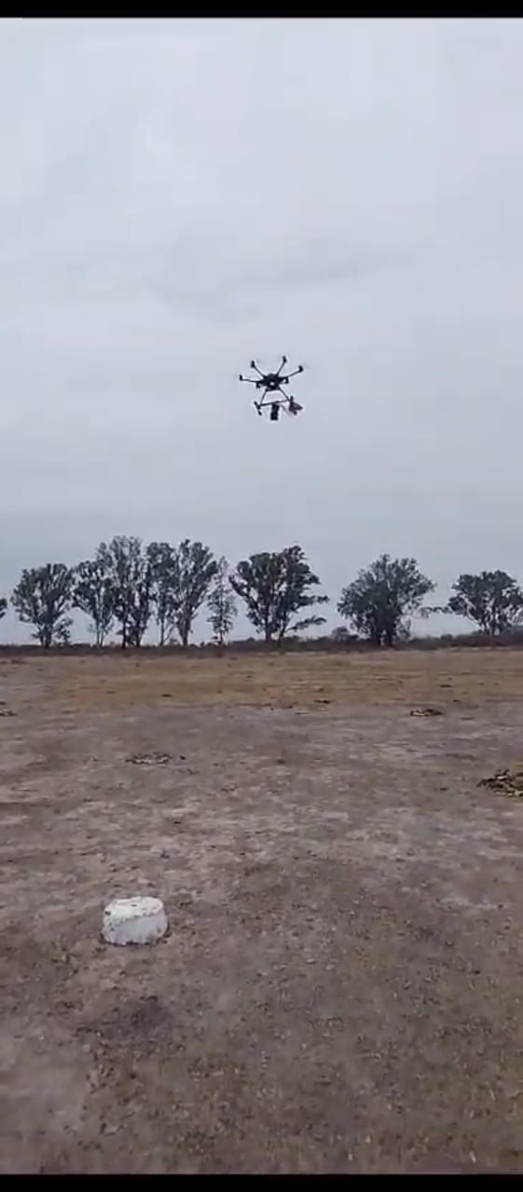
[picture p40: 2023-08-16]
assets/test/dron_subida.jpg

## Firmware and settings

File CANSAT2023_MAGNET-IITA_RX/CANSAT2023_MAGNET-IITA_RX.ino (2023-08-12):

/*********
  Modified from the examples of the Arduino LoRa library
  More resources: https://randomnerdtutorials.com

  Adaptado por Matias Graiño LU9CBL, LU1CJM, LU1AET, LU6APA
  23/05/2022 adecuaciones LU6APA
  27/05/2022 adecuaciones LU6APA
  28/03/2023 adecuaciones LU6APA y LU4BA
*********/

#include <SPI.h>
#include <LoRa.h>

char Version[] = "v2.6 - 15/03/2023";

//Defino los pines a ser usados por el modulo transceptor LoRa
#define CS    18      // Pin de CS del módulo LoRa
#define RST   14      // Pin de Reset del módulo LoRa
#define IRQ   7      // Pin del IRQ del módulo LoRa
#define LED   25     // Pin del LED onboard

#define SERIAL_BAUDRATE   115200    // Velocidad del Puerto Serie

// Configuraciones del módulo LoRa. Tener en cuenta que esta configuración debe ser igual en el Rx!
// 433E6 for Asia
// 866E6 for Europe
// 915E6 for North America 
// 915E6 to 928E3 for Argentina
#define LORA_FREQUENCY      915000000  // Frecuencia en Hz a la que se quiere transmitir.
#define LORA_SYNC_WORD      0xF3       // Byte value to use as the sync word, defaults to 0x12
#define LORA_POWER          17         // TX power in dB, defaults to 17. Supported values are 2 to 20 for PA_OUTPUT_PA_BOOST_PIN, and 0 to 14 for PA_OUTPUT_RFO_PIN.
#define LORA_SPREAD_FACTOR  7          // Spreading factor, defaults to 7. Supported values are between 6 and 12 (En Argentina se puede utilizar entre 7 a 10)
#define LORA_SIG_BANDWIDTH  125E3      // Signal bandwidth in Hz, defaults to 125E3. Supported values are 7.8E3, 10.4E3, 15.6E3, 20.8E3, 31.25E3, 41.7E3, 62.5E3, 125E3, 250E3, and 500E3 
#define LORA_CODING_RATE    5          // Denominator of the coding rate, defaults to 5. Supported values are between 5 and 8, these correspond to coding rates of 4/5 and 4/8. The coding rate numerator is fixed at 4.

double bitRate;


void setup() 
{  
  // Set Led onboard con Output
  pinMode(LED, OUTPUT);
  
  //Incializo el Serial Monitor
  Serial.begin(SERIAL_BAUDRATE);
  
  while (!Serial) 
  {
    // Mientras el COM no esté disponible el LED onbooard encendido
    digitalWrite(LED, HIGH);  
  }

  // Apaga el LED si se conecta al COM
  digitalWrite(LED, LOW);  
  
  Serial.println("LoRa Receiver");

  // Inicializar módulo LoRa
  LoRa.setPins(CS, RST, IRQ);
  while (!LoRa.begin(LORA_FREQUENCY)) 
  {
    Serial.println(".");
    delay(500);
  }
  
  // Change sync word (0xF3) to match the receiver
  // The sync word assures you don't get LoRa messages from other LoRa transceivers
  // ranges from 0-0xFF
  LoRa.setSyncWord(LORA_SYNC_WORD);
  LoRa.setTxPower(LORA_POWER);              
  LoRa.setSpreadingFactor(LORA_SPREAD_FACTOR);           
  LoRa.setSignalBandwidth(LORA_SIG_BANDWIDTH);
  LoRa.setCodingRate4(LORA_CODING_RATE);  
  
  // Calculo del BitRate = (SF * (BW / 2 ^ SF)) * (4.0 / CR)
  bitRate = (LORA_SPREAD_FACTOR * (LORA_SIG_BANDWIDTH / pow(2, LORA_SPREAD_FACTOR))) * (4.0 / LORA_CODING_RATE);
  
  Serial.println("LoRa Initializing OK!");  
}


void loop() 
{
  // Version v2.6 - 15/03/2023
  // LoRa BitRate: 5468.75 bps
  // Telemetria RAW Recibida 530,1014.66,1014.56,0.81,22.15
  // Packet Number: 530
  // Presion Base: 1014.66
  // Presion Absoluta: 1014.56
  // Altura: 0.81
  // Temperatura: 22.15
  // Nivel de señal [RSSI]: -45
  // =====================================================================
  
  // Trato de parsear el paquete  
  int packetSize = LoRa.parsePacket();
  
  if (packetSize) 
  {     
    // Encender LED onboard
    digitalWrite(LED, HIGH);  
  
    // Paquete recibido
    // Lectura del paquete
    while (LoRa.available()) 
    {
      String LoRaData = LoRa.readString();
      // Serial.println(LoRaData);
      
      //Serial.print("RX - Version ");     
      //Serial.println(Version);      
  
      //Serial.print("LoRa BitRate: ");
      //Serial.print(bitRate);
      //Serial.println(" bps");
            
      //Serial.print("Telemetria RAW Recibida ");
      //Serial.println(LoRaData); 
        
      int indicador1 = LoRaData.indexOf(',');
      String pktNumber = LoRaData.substring(0, indicador1);
      //Serial.print("Packet Number: ");
      //Serial.println(pktNumber);
      
      int indicador2 = LoRaData.indexOf(',', indicador1+1);
      String presionBase = LoRaData.substring(indicador1+1, indicador2);
      //Serial.print("Presion Base: ");
      //Serial.println(presionBase);

      int indicador3 = LoRaData.indexOf(',', indicador2+1);
      String presionAbsoluta = LoRaData.substring(indicador2+1, indicador3);
      //Serial.print("Presion Absoluta: ");
      //Serial.println(presionAbsoluta);

      int indicador4 = LoRaData.indexOf(',', indicador3+1);
      String altura = LoRaData.substring(indicador3+1, indicador4);
      //Serial.print("Altura: ");
      //Serial.println(altura);  
        
      int indicador5 = LoRaData.indexOf(',', indicador4+1);
      String temperatura = LoRaData.substring(indicador4+1, indicador5);
      //Serial.print("Temperatura: ");
      //Serial.println(temperatura);
      
      int indicador6 = LoRaData.indexOf(',', indicador5+1);
      String MagneX = LoRaData.substring(indicador5+1, indicador6);

      int indicador7 = LoRaData.indexOf(',', indicador6+1);
      String MagneY = LoRaData.substring(indicador6+1, indicador7);

      int indicador8 = LoRaData.indexOf(',', indicador7+1);
      String MagneZ = LoRaData.substring(indicador7+1, indicador8);
      
      // Message to print in Serial port
    //Serial.println("[Packet Number],[Presion Base],[Presion Absoluta],[Altura],[Temperatura],");
      Serial.println(pktNumber + "," + presionBase + "," + presionAbsoluta + "," + altura + "," + temperatura + "," + MagneX + "," + MagneY + "," + MagneZ);  
    }
    
    // Nivel de señal RSSI del paquete
    //Serial.print("Nivel de señal [RSSI]: ");
    //Serial.println(LoRa.packetRssi());
    //Serial.println("=====================================================================");


    
    // Apagar LED onboard
    digitalWrite(LED, LOW); 
  }
}

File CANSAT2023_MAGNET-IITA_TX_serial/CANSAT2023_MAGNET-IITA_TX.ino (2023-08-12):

/*
  Mision MagnetIITA - CanSat Argentina 2023
  Diagrama de Conexion: 

 SDAMPU = 4
 SCLMPU = 15

 SDABMP = 22
 SCLBMP = 21
  
*/
#include <Wire.h>
#include <SPI.h>
#include <LoRa.h>
#include <Adafruit_BMP085.h>
///////////////////////////////////////////////////////
#include <MPU9250_WE.h>
#define MPU9250_ADDR 0x68
MPU9250_WE myMPU9250 = MPU9250_WE(&Wire1, MPU9250_ADDR);
///////////////////////////////////////////////////////
Adafruit_BMP085 bmp;

char Version[] = "v2.6 - 28/03/2023";

#define CS    18      // Pin de CS del módulo LoRa
#define RST   14      // Pin de Reset del módulo LoRa
#define IRQ   7      // Pin del IRQ del módulo LoRa
#define LED   25     // Pin del LED onboard

#define SERIAL_BAUDRATE   115200    // Velocidad del Puerto Serie

#define INTERVAL_TIME_TX  1000    // Cantidad de Segundos entre cada TX

// Configuraciones del módulo LoRa. Tener en cuenta que esta configuración debe ser igual en el Rx!
// 433E6 for Asia
// 866E6 for Europe
// 915E6 for North America 
// 915E6 to 928E3 for Argentina
#define LORA_FREQUENCY      915000000  // Frecuencia en Hz a la que se quiere transmitir.
#define LORA_SYNC_WORD      0xF3       // Byte value to use as the sync word, defaults to 0x12
#define LORA_POWER          17         // TX power in dB, defaults to 17. Supported values are 2 to 20 for PA_OUTPUT_PA_BOOST_PIN, and 0 to 14 for PA_OUTPUT_RFO_PIN.
#define LORA_SPREAD_FACTOR  7          // Spreading factor, defaults to 7. Supported values are between 6 and 12 (En Argentina se puede utilizar entre 7 a 10)
#define LORA_SIG_BANDWIDTH  125E3      // Signal bandwidth in Hz, defaults to 125E3. Supported values are 7.8E3, 10.4E3, 15.6E3, 20.8E3, 31.25E3, 41.7E3, 62.5E3, 125E3, 250E3, and 500E3 
#define LORA_CODING_RATE    5          // Denominator of the coding rate, defaults to 5. Supported values are between 5 and 8, these correspond to coding rates of 4/5 and 4/8. The coding rate numerator is fixed at 4.

double baseline;
double T, P, A;
unsigned int pktNumber = 0;
double bitRate;

void setup()
{
  // Set de Serial
  Serial.begin(SERIAL_BAUDRATE);
  
  // Set Led onboard con Output
  pinMode(LED, OUTPUT);

  // Set de pin RST como Output y se pone a High para que pueda operar
  pinMode(RST, OUTPUT);
  digitalWrite(RST, HIGH);  
    
  //Inicializar módulo LoRa
  LoRa.setPins(CS, RST, IRQ);
    
  while (!LoRa.begin(LORA_FREQUENCY)) 
  {
      Serial.println(".");
      delay(500);
  }
  
  LoRa.setTxPower(LORA_POWER);              
  LoRa.setSpreadingFactor(LORA_SPREAD_FACTOR);           
  LoRa.setSignalBandwidth(LORA_SIG_BANDWIDTH);
  LoRa.setCodingRate4(LORA_CODING_RATE);       
  LoRa.setSyncWord(LORA_SYNC_WORD);    

  // Calculo del BitRate = (SF * (BW / 2 ^ SF)) * (4.0 / CR)
  bitRate = (LORA_SPREAD_FACTOR * (LORA_SIG_BANDWIDTH / pow(2, LORA_SPREAD_FACTOR))) * (4.0 / LORA_CODING_RATE);

  Serial.println("LoRa OK!");
  
  // Inicializar el BMP180
  bool bmpIsInit = false;
  
  Serial.println("Iniciando BMP180 ");

  // Si el BMP180 no inicializa, no arranca la placa y el led onboard queda encendido! 
  digitalWrite(LED, HIGH); 
  
  do {
        delay(100);  
        Wire.begin(22,21);
        if (bmp.begin(BMP085_STANDARD))
        {
              Serial.println("BMP180 inicio OK");
              readTempPressure();
              baseline = P;
              Serial.print("Presion Base: ");
              Serial.print(baseline);
              Serial.println(" hpa");
              bmpIsInit = true;
              digitalWrite(LED, LOW); 
        } 
        else
        {
          Serial.println("No entro :-(");
        }     
        
      } while (!bmpIsInit);

      /////////////////////////////////////////////////////////
      Wire1.begin(4,15);
  if(!myMPU9250.init()){
    Serial.println("MPU9250 does not respond");
  }
  else{
    Serial.println("MPU9250 is connected");
  }
  if(!myMPU9250.initMagnetometer()){
    Serial.println("Magnetometer does not respond");
  }
  else{
    Serial.println("Magnetometer is connected");
  }
  myMPU9250.setMagOpMode(AK8963_CONT_MODE_100HZ);
      /////////////////////////////////////////////////////////
  
}

void loop()
{
  // // Version v2.5 - 27/05/2022
  // // LoRa BitRate: 5468.75 bps
  // // Temperatura:  22.088 °C 
  // // Presion Base: 1015.081 hpa
  // // Presion Absoluta: 1014.979 hpa | 761.299 mmHg | 14.721 psi
  // // Altura:  0.843 m, 
  // // Packet Number: 641
  // // Enviando datos: [Packet Number],[Presion Base],[Presion Absoluta],[Altura],[Temperatura]
  // // 641,1015.081,1014.979,0.843,22.088
  // // =====================================================================
  
  // Leer Presion, Temperatura y calcular Altura
  readTempPressure();

  Serial.print("TX - Version ");
  Serial.println(Version);

  Serial.print("LoRa BitRate: ");
  Serial.print(bitRate);
  Serial.println(" bps");
    
  Serial.print("Temperatura: ");
  if (T >= 0.0) Serial.print(" ");
  Serial.print(T, 1);
  Serial.println(" °C ");
     
  Serial.print("Presion Base: ");
  Serial.print(baseline * 0.01);
  Serial.println(" hpa");
      
  Serial.print("Presion Absoluta: ");
  Serial.print(P * 0.01, 2);
  Serial.print(" hpa | ");
  Serial.print(P * 0.750063755);
  Serial.print(" mmHg | ");
  Serial.print(P * 0.014503774);
  Serial.println(" psi"); 
  
  Serial.print("Altura: ");
  if (A >= 0.0) Serial.print(" ");
  Serial.print(A, 2);
  Serial.println(" m, ");

  pktNumber++;  
  Serial.print("Packet Number: ");
  Serial.println(pktNumber);
  
  Serial.println("Enviando datos: [Packet Number],[Presion Base],[Presion Absoluta],[Altura],[Temperatura]");
  Serial.print(pktNumber);
  Serial.print(",");
  Serial.print(baseline * 0.01);
  Serial.print(",");
  Serial.print(P * 0.01, 2);
  Serial.print(",");
  Serial.print(A, 2);
  Serial.print(",");
  Serial.println(T, 1);  

   ///////////////////////
  xyzFloat magValue = myMPU9250.getMagValues(); // returns magnetic flux density [µT] 

  Serial.println("Datos magnetometro en µTesla: ");
  Serial.print(magValue.x);
  Serial.print("   ");
  Serial.print(magValue.y);
  Serial.print("   ");
  Serial.println(magValue.z);
   
   //////////////////////
  //Send LoRa packet to receiver
  digitalWrite(LED, HIGH);    
  
  //Serial.println("POR ENTRAR AL LORA");
  LoRa.beginPacket();
  LoRa.print(pktNumber); 
  LoRa.print(","); 
  LoRa.print(baseline * 0.01);
  LoRa.print(",");
  LoRa.print(P * 0.01, 2);
  LoRa.print(",");
  LoRa.print(A, 2);
  LoRa.print(",");
  LoRa.print(T, 1);
  LoRa.print(",");
  LoRa.print(magValue.x);
  LoRa.print(",");
  LoRa.print(magValue.y);
  LoRa.print(",");
  LoRa.print(magValue.z);
  LoRa.endPacket();
  
  digitalWrite(LED, LOW);

  // Volver a 0 para que no haga overflow
  if (pktNumber >= 65500)
  {
    pktNumber = 0;
  }
  
  Serial.println("=====================================================================");

  // Tiempo de espera entre Tx y Tx
  delay(INTERVAL_TIME_TX);
}
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

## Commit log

2023-08-12 add first version of thing for Magnet-IITA
2023-08-14 add some files 3d and cloud
    [BASE.stl, PIEZA v1.stl, Sin título v1.stl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]
2023-08-16 add description of construction and ground station
